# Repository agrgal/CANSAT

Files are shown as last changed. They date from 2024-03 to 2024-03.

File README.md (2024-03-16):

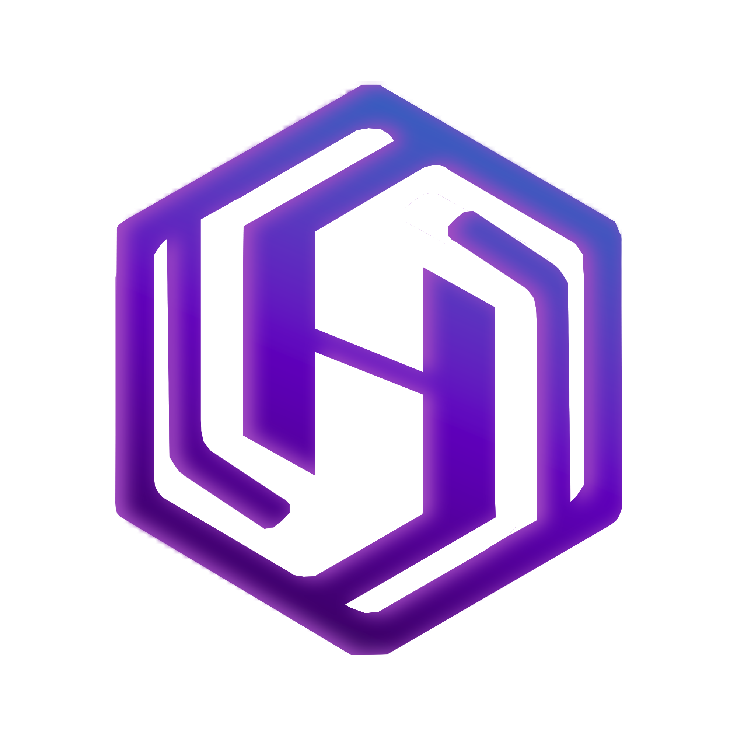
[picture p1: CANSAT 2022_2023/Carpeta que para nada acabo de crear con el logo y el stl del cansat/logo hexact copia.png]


# CANSAT - A4I y HEXACT
Proyectos CANSAT IES Seritium, año 2022 y 2023, presentados a los lanzamientos en la comunidad autónoma de Andalucía en Coria del Río y Antequera. Copia pública

# Reconocimiento
[CANSAT IES Seritium](https://github.com/CANSAT) © 2023 by Alejandro Chacón, David González, Antonio Jesús Suarez, Adrián Durán, Miriam Ganaza, Iker Espinosa y Aurelio Gallardo is licensed under [CC BY-NC-SA 4.0 ](http://creativecommons.org/licenses/by-nc-sa/4.0/?ref=chooser-v1)

# ¿Qué es?
El proyecto CANSAT (HEXACT en 2023, A4I en 2022) llevado a cabo por los alumnos Alejandro Chacón, David González, Antonio Jesús Suarez, Adrián Durán, Miriam Ganaza e Iker Espinosa del IES Seritium. Como mentor, Aurelio Gallardo. 

# ¿Qué contiene este documento?
Informe crítico de diseño y todo aquel material elaborado para llevar a cabo el proyecto (diseño, pruebas, programación, informes, resultados) de nuestra participación en las pruebas andaluzas de los años 2022 y 2023

# Material gráfico
+ [Vídeo presentación del proyecto 2023](https://youtu.be/i_LCr1teCZs?si=MErtpM3VWjnIBio4)
+ [Lanzamiento Mayo 2023](https://www.youtube.com/watch?v=RIHoM7wkHl4)
+ [Noticia diario de Jerez](https://www.diariodejerez.es/jerez/IES-Seritium-Agencia-Espacial-Europea-cansat_0_1791421220.html)
+ [CANSAT 2022](https://www.seritium.es/wordpress/index.php/2022/03/24/proyecto-cansat-2022/)

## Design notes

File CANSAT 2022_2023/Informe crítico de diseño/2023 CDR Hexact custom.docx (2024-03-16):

# HEXACT -CDR

(Critical Design Review)

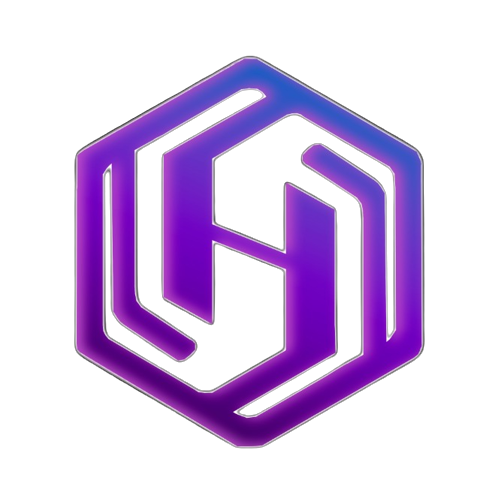
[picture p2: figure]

# Índice:

Índice: 1

Introducción: 2

El equipo: 2

Objetivos de la misión. 2

Vídeo presentación. 2

Misión primaria y secundaria. 3

Misión primaria. 3

Medida de presión y temperatura. 3

Diseño del paracaídas. 4

Análisis de datos 5

Diseño del CanSat 5

Misión secundaria 7

Dispersor de semillas. 7

Localización del dispositivo. 7

Planificación 8

Presupuesto 8

Plan de difusión y patrocinio 10

Notas 10

# Introducción:

## El equipo:

- Alejandro Chacón Pérez → Códigos del satélite y las estaciones tierra, diseño de la electrónica.
- David González Diosdado → Código processing, análisis de datos y ayuda en diseño en 3D.
- Antonio Jesús Suarez Gómez→ Diseño en 3D, soldadura y montaje de las antenas.
- Adrián Durán Perdigones→ Edición de los videos introductorios y diseño del logo.
- Miriam Ganaza Gómez→ Diseño y fabricación del paracaídas.
- Iker Espinosa Algeciras → Ayuda con las redes sociales.

Profesor responsable: Aurelio Gallardo (aurelio@seritium.es).

Instituto IES Seritium (11700767) - Jerez de la Frontera

## Objetivos de la misión.

Nuestros objetivos son:

1. Análisis con precisión de las condiciones medioambientales (Presión y temperatura) de la zona de lanzamiento.
2. Dispersión de semillas controlada durante el vuelo.
3. Análisis del estado del satélite durante el vuelo y recuperación para su reutilización una vez finalizada la misión.
4. Crear una base de datos didáctica para ayudar e incentivar a futuras generaciones de estudiantes que decidan participar en el proyecto CanSat.
5. Divertirnos y aprender.

## Vídeo presentación.

Vídeo presentación de nuestro proyecto CanSat. (https://youtu.be/FIYeHxksmDY)

# Misión primaria y secundaria.

El esquema de vuelo del proyecto se divide en 2 partes:

1. Recogida y procesamiento de datos, así como expulsión periódica de semillas, que toma lugar en el CanSat
2. Recibo y procesamiento de dichos datos, que incluye: Desencriptado, almacenamiento en la tarjeta SD, mostrado por pantalla y post-procesamiento en Processing para obtener la posición y tablas de los datos.

Los datos que recogeremos serán almacenados en la tarjeta SD, e incluyen: Temperatura, presión (y derivada, la altura), aceleración, ángulo de inclinación y distancia satélite-base.

Utilizamos, como placa procesadora, una ESP32 v4, que nos da una gran capacidad de procesamiento y un alto número de pines útiles. Elaboramos, asimismo, una PCB personalizada, que nos permite montar todos los sensores y componentes de manera segura y eficiente.

Para la estación de tierra, decidimos usar la placa de desarrollo LILYGO T-BEAM ESP32, que, además de proporcionarnos multitud de pines con los que trabajar, dispone, de manera integrada, de módulo de radio Lora y de chip GPS, muy útiles para el funcionamiento de muestras misiones primarias y secundarias.

Todo el proyecto, tanto el dispositivo CanSat como las estaciones de tierra, han sido programados en Arduino, usando la IDE 2.0.3 oficial.

## Misión primaria.

### Medida de presión y temperatura.

Como misión primaria, encontramos la medida de presión y temperatura. Conseguiremos estos datos con el sensor GY-87, ubicado en el interior de la carcasa del CanSat. A través del módulo LoRa de telecomunicaciones, enviamos los datos a las estaciones de tierra en forma de un sólo paquete con toda la información (Tanto de la misión primaria como secundaria) concatenada.

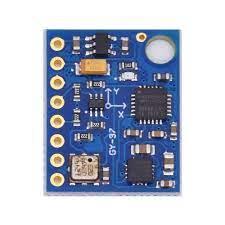
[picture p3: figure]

Elegimos este sensor porque, aparte de las medidas de temperatura y presión, nos proporciona también datos de aceleración y giroscopio, muy útiles para conocer el estado del satélite en su descenso, todo condensado en un sólo sensor.

Los programas siguen los siguientes esquemas. Diferenciamos entre el programa del satélite y el programa de las estaciones de tierra.

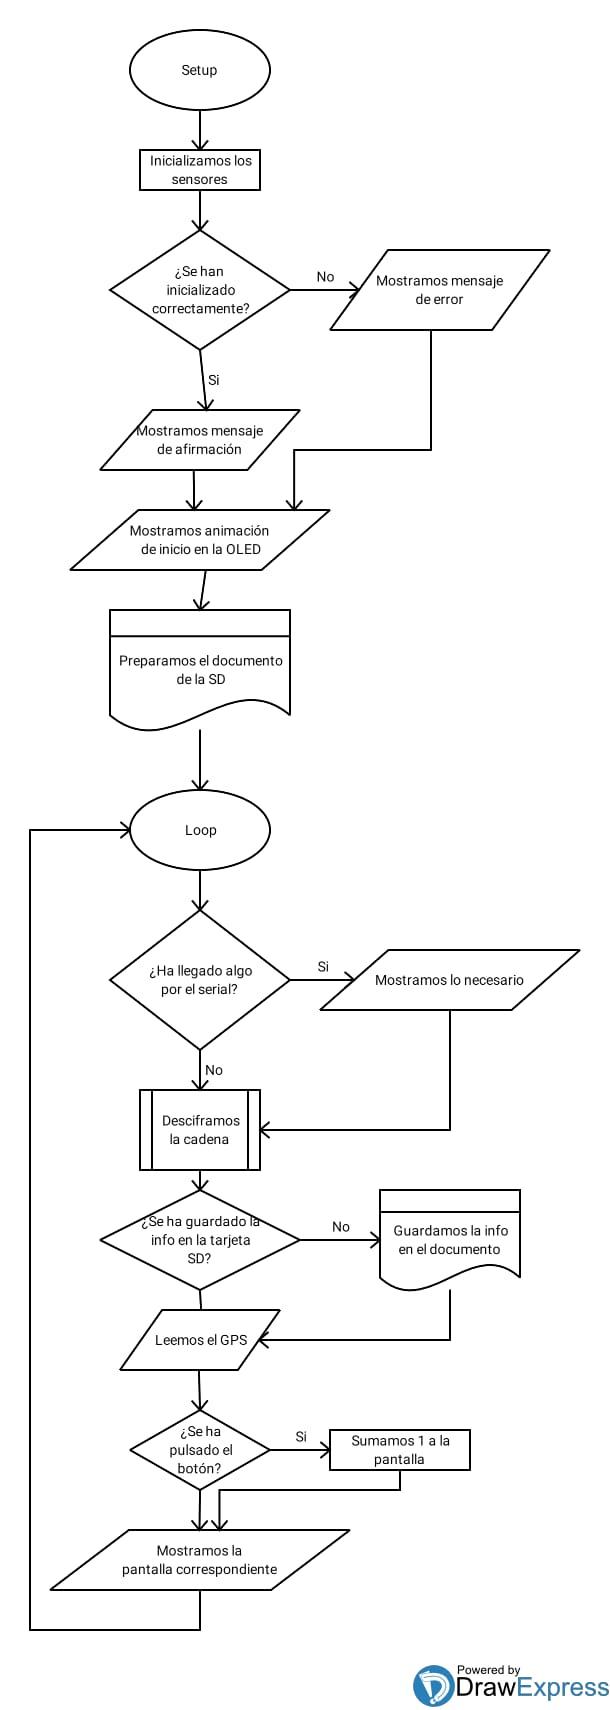
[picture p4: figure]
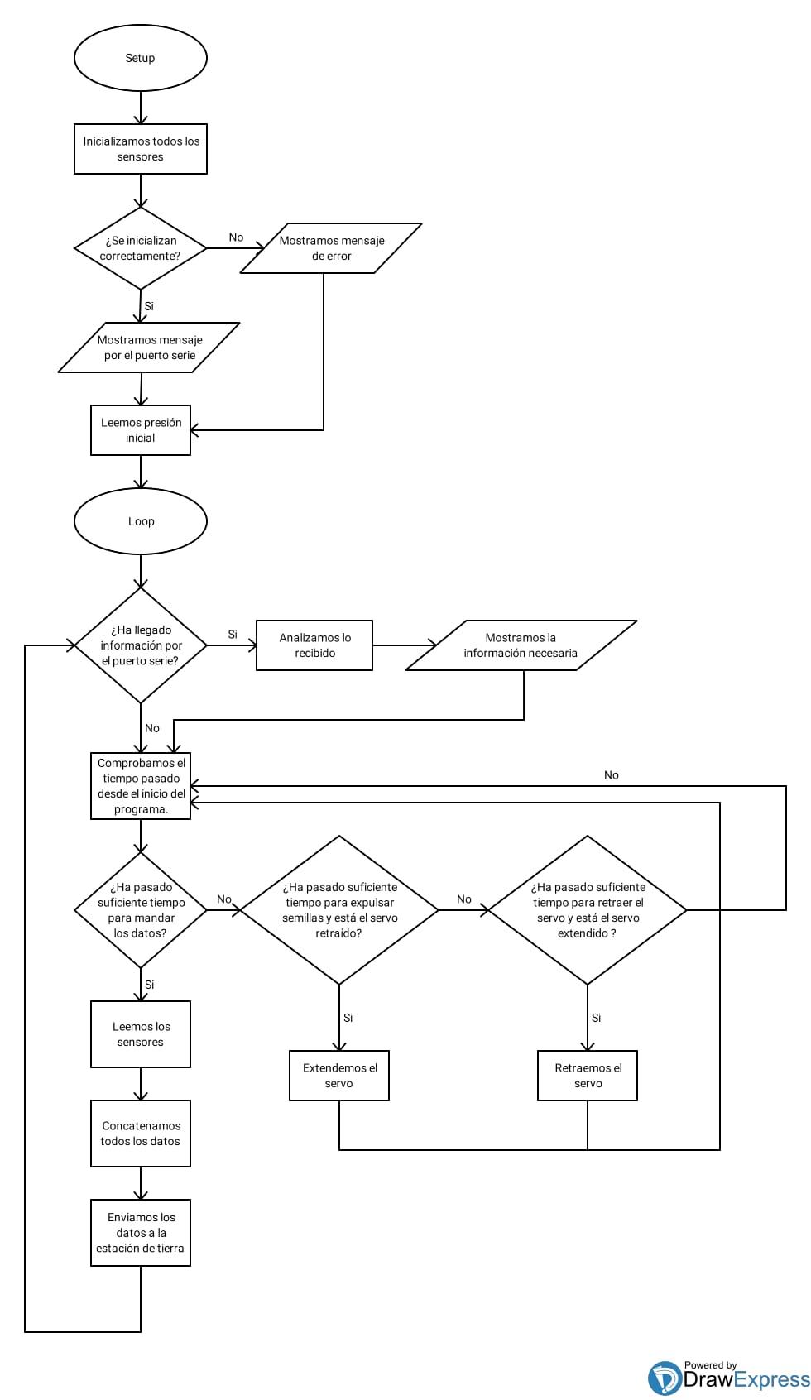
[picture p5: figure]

### Diseño del paracaídas.

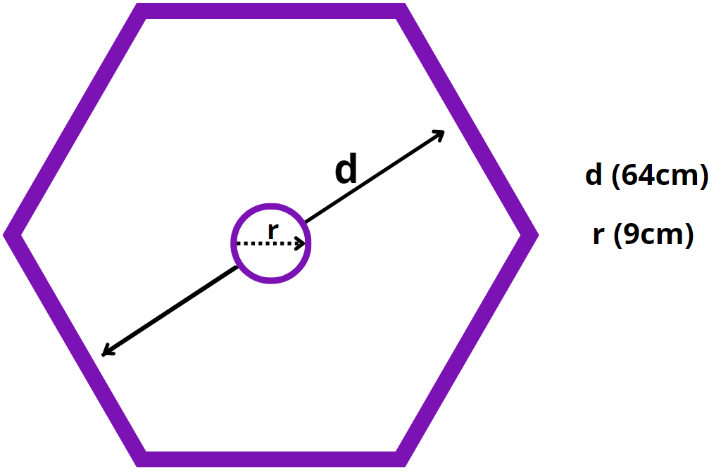
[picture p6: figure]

Teniendo como referencia nuestro proyecto CanSat de anteriores ediciones, decidimos rediseñar nuestro prototipo de paracaídas para que cayera de forma más rápida y precisa, aun conservando una velocidad regulada para evitar un impacto fatal.

El paracaídas está fabricado con tela especializada de paracaídas, con cuerda de tanza reforzada para unirla al CanSat. Sacamos la superficie necesaria para nuestro paracaídas igualando la fuerza gravitatoria con la de arrastre, teniendo en cuenta el peso deseado y la velocidad a la que queríamos que descendiese, para que nuestro aterrizaje sea rápido pero eficaz. Además, decidimos cambiar la forma anterior del paracaídas y hacerlo un hexágono, ya que así conseguimos reducir el uso de materiales aun sujetando la misma cantidad de peso.

### Análisis de datos

Los datos recogidos, una vez desencriptados y almacenados en la tarjeta SD de cada base, serán exportados al programa de Processing, que se encargará de mostrar, en distintas tablas 2D y 3D, los distintos datos, la posición mediante coordenadas, la angulación con un modelo 3d que se gira dependiendo de los datos recibidos y la presión y temperatura en una gráfica separada. Asimismo, y usando la distancia a cada estación, calcularemos la posición relativa del dispositivo, que se mostrará con los otros datos y será usada para la rápida y eficiente recuperación del CanSat. Estas son dos ejemplos de gráficas hechas con Processing con algunos datos de prueba:

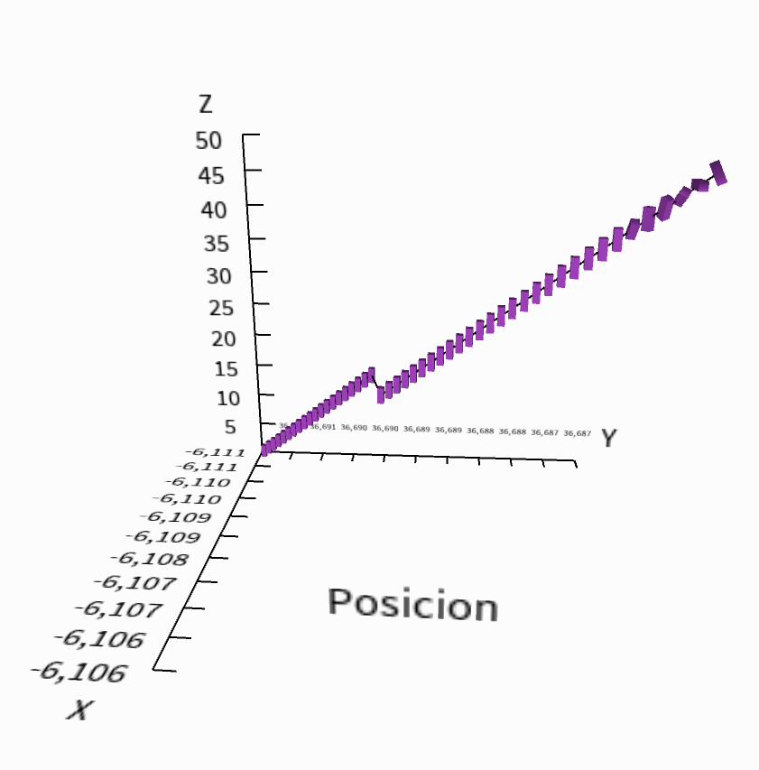
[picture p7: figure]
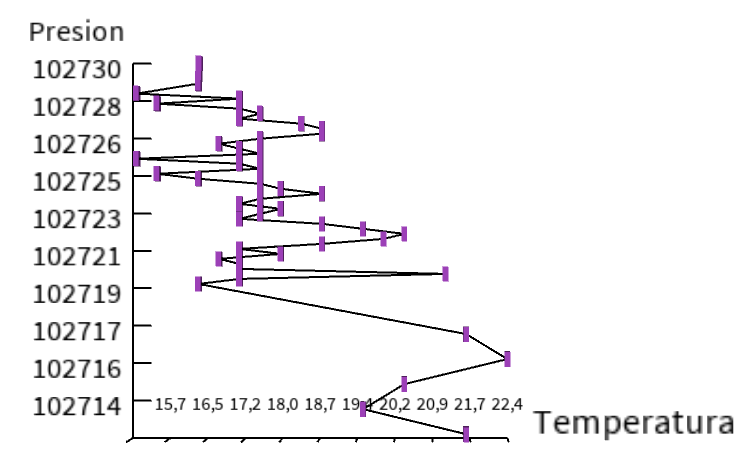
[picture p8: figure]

## Diseño del CanSat

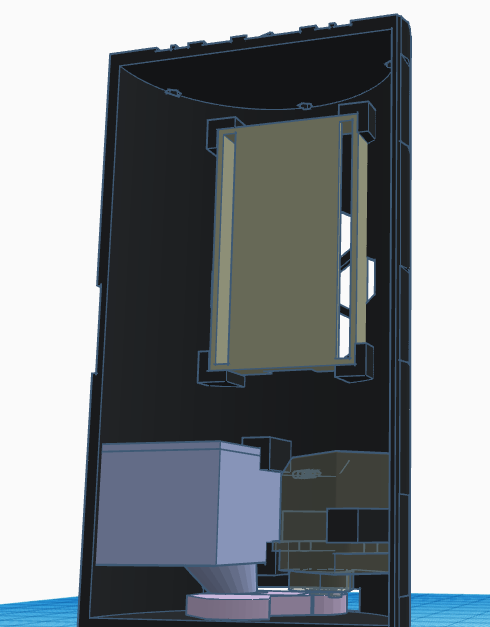
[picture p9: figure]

Peso aproximado: 312g , a falta de algunas modificaciones.

La carcasa de nuestro prototipo ha sido diseñada para dar cabida a los sensores, la placa ESP32, una batería 18650 y al mecanismo de eyección de semillas. La placa y los sensores están colocados en la parte superior, montados en la PCB personalizada en forma de “sandwich” (pieza colocada en el modelo color beige), para aprovechar al máximo el espacio útil. La PCB ha sido diseñada con esta configuración en mente, para posicionar los sensores y los pines de alimentación de la manera más eficiente posible.

En el centro de la PCB encontraremos el sistema de telecomunicaciones (Lora). En la parte inferior encontramos el servo (Transparente naranja), el cual mueve el brazo (rosa) que deja caer las semillas, depositadas desde el tanque (azul)

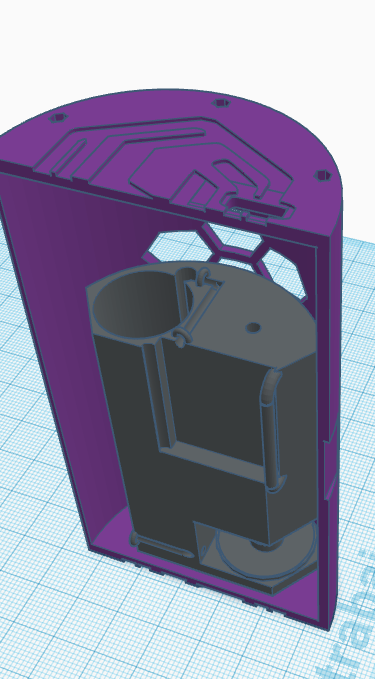
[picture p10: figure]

En la otra mitad encontraremos un modelo de donde va insertada la batería (18650), su respectivo módulo de carga ,y de forma perpendicular a la base, la antena que irá conectada al Lora. Estos componentes se encuentran en la mitad inferior para proporcionar más estabilidad durante el descenso, colocando la mayor cantidad de masa lo más bajo posible para alterar el centro de gravedad.

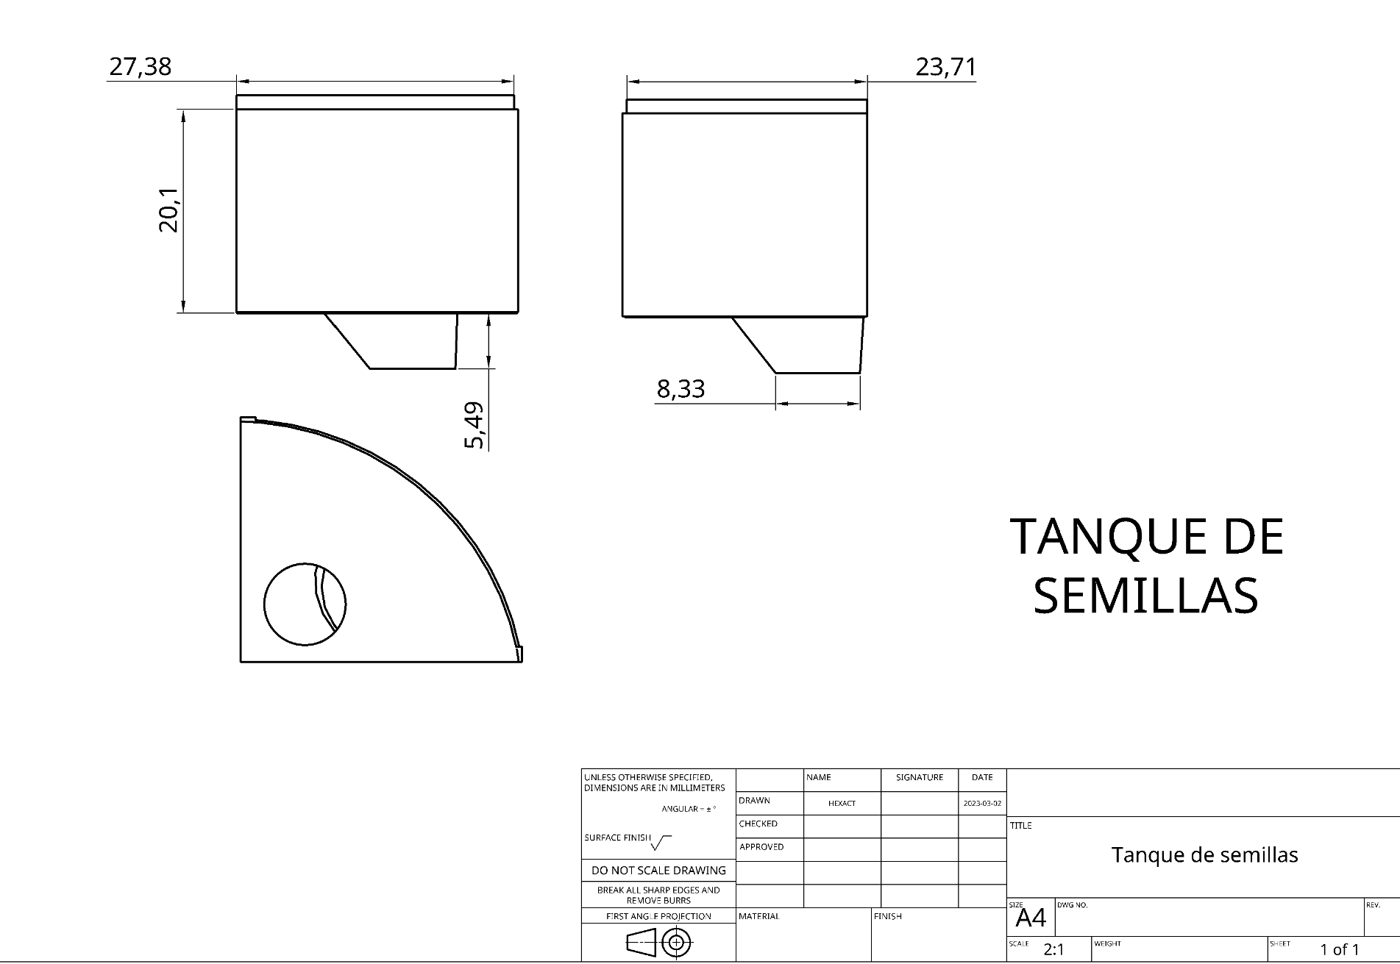
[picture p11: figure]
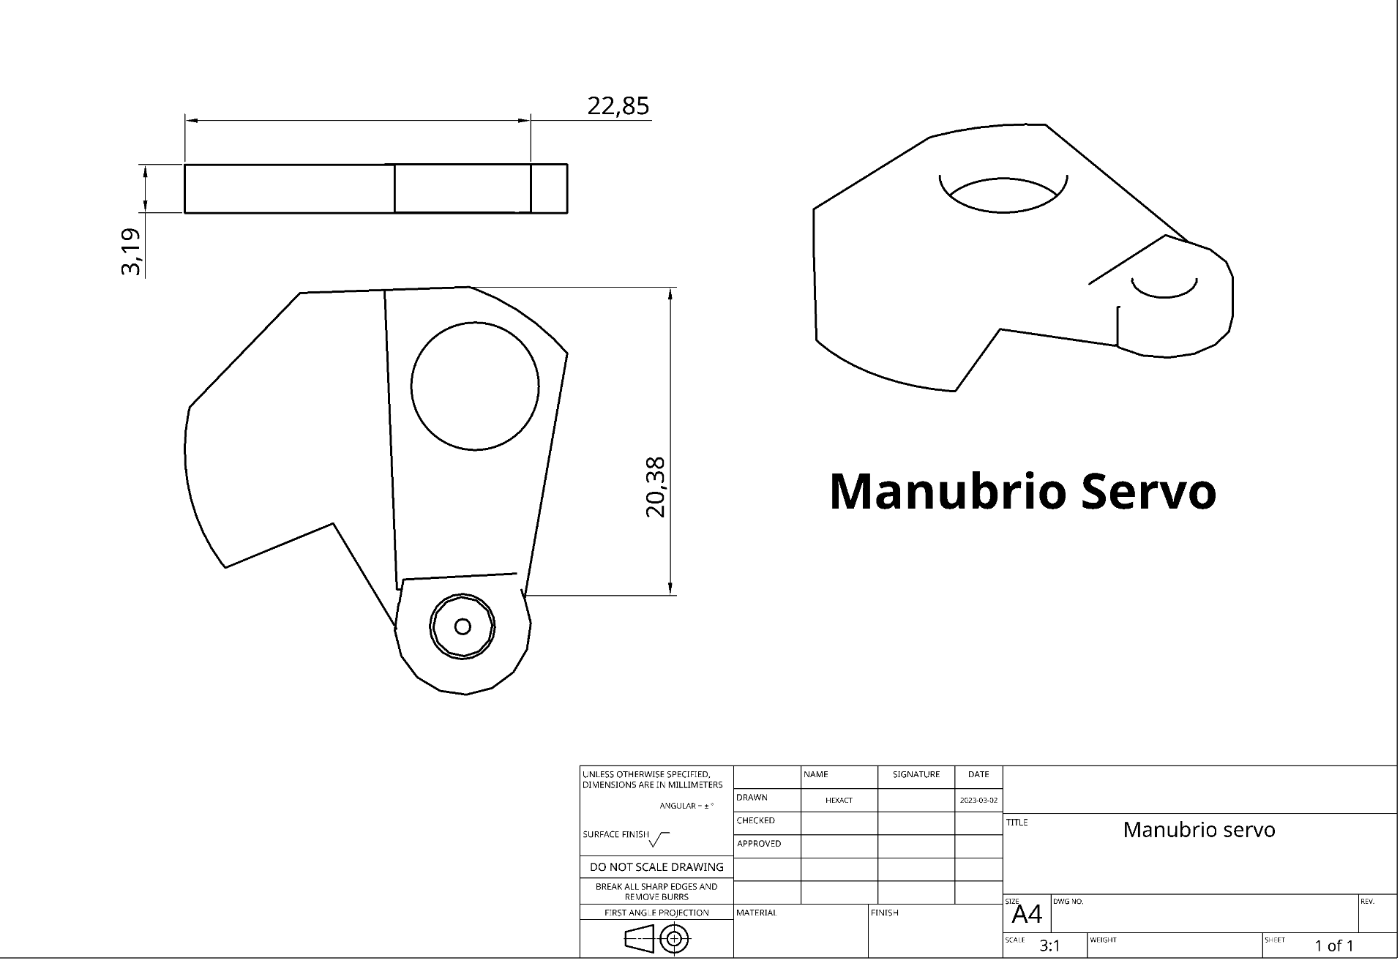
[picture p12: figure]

En los laterales exteriores, diseñamos unas hendiduras donde colocar bisagras metálicas, que proporcionan mayor resistencia al prototipo, aun manteniendo la funcionalidad de cofre.

El dispositivo está diseñado con facilidad de uso en mente: Dispondrá de salidas USB al exterior que permiten tanto recargar las baterías interiores como acceder a la placa directamente para su reprogramación o ajustes vía comunicación serie del propio programa. Lo ideamos todo para que pueda servir como base para futuras generaciones de participantes de CanSat y como elemento didáctico a la hora de enseñar programación, diseño y electrónica.

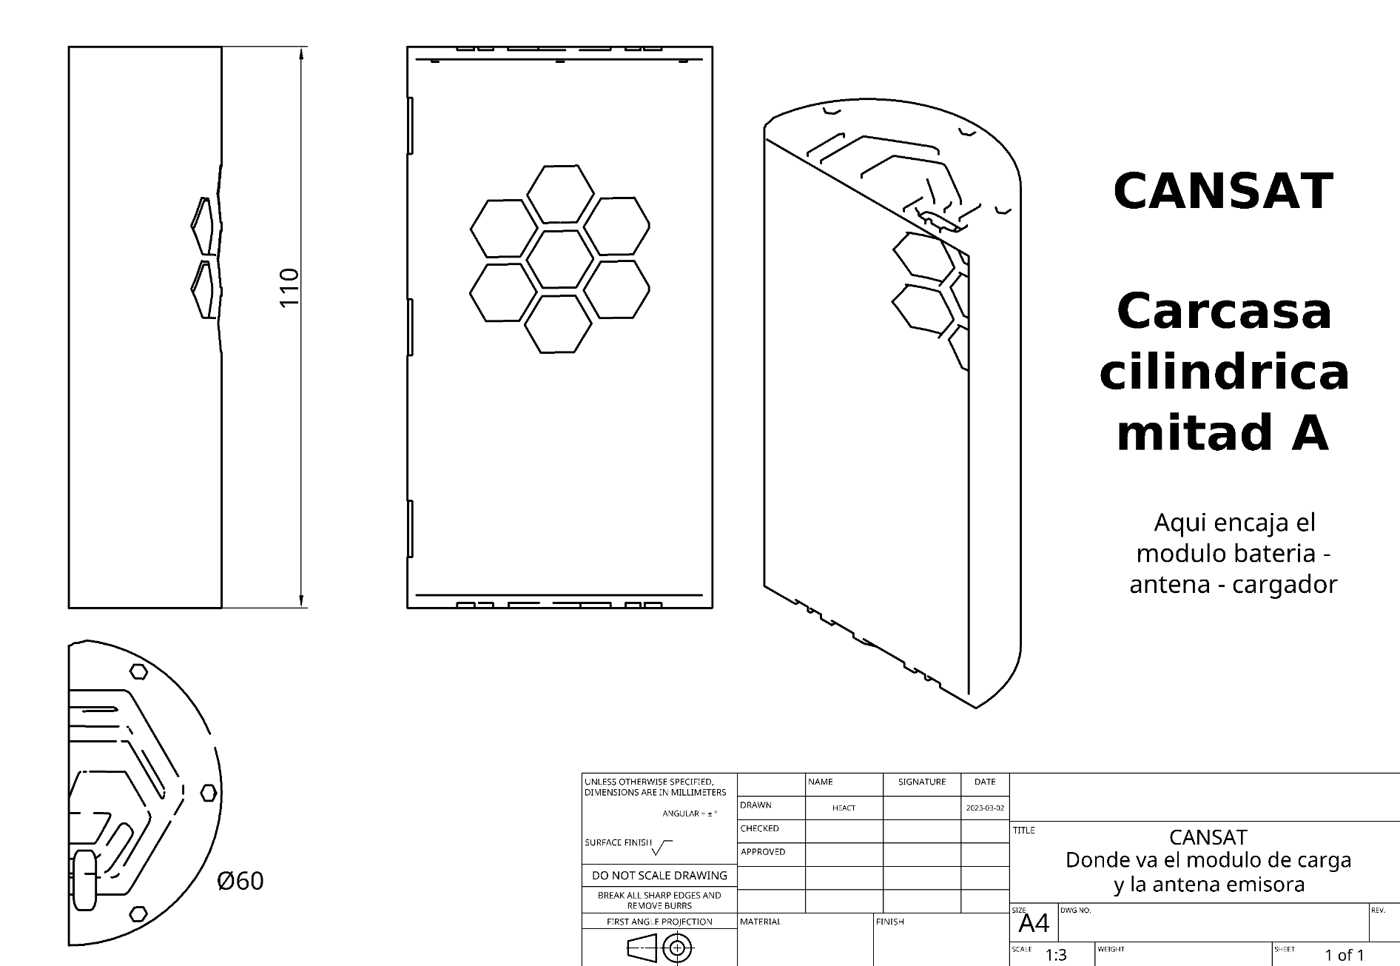
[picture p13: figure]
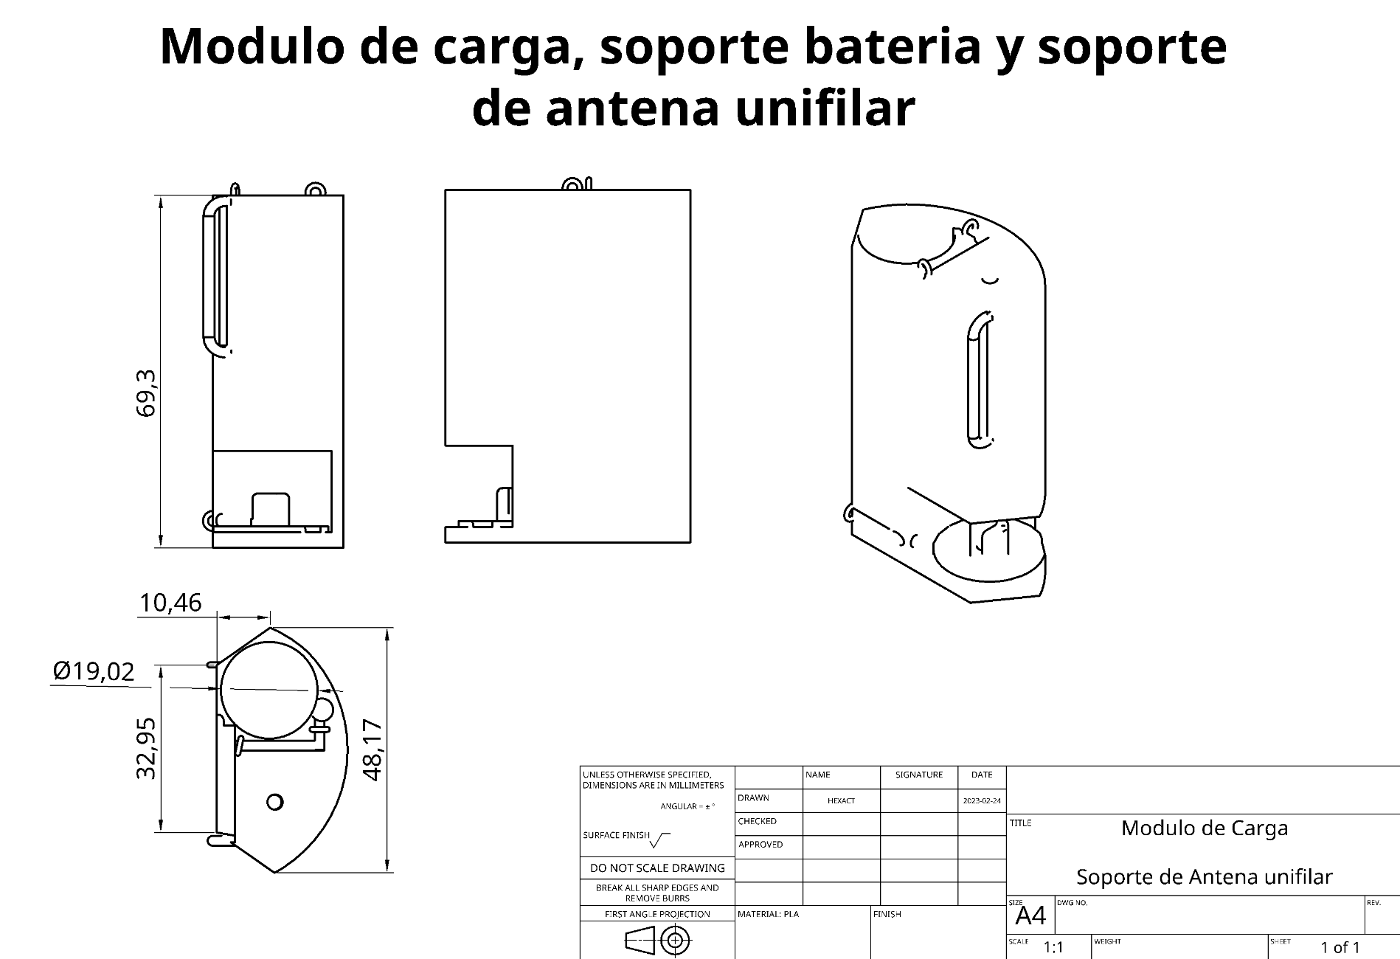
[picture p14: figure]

La antena también ha sido diseñada e impresa en 3D, con especial cuidado en mantener las medidas correctas para antenas Yagi pero con un diseño práctico: Está formada por partes desmontables para facilitar su almacenaje, y dispone de 2 mangos para poder sujetarla cómodamente .

## Misión secundaria

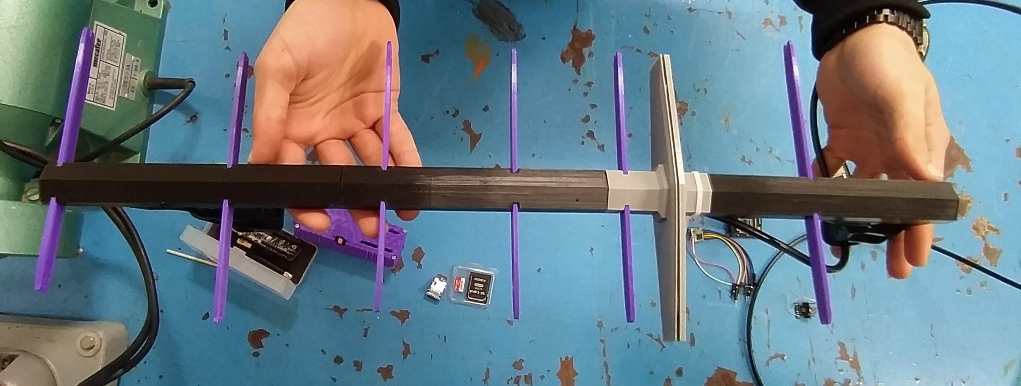
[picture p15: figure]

Nuestra misión secundaria se compone de 2 partes. La primera es un sistema de dispersión de semillas, que expulsa semillas periódicamente. Nuestro segundo proyecto científico es la localización del dispositivo sin uso de tecnologías GPS.

### Dispersor de semillas.

El sistema de dispersión de semillas consiste en un depósito con semillas, un brazo móvil y un servo que realiza el trabajo. Las semillas caen en el brazo por acción de la gravedad. El servo, periódicamente, se mueve, dejando caer las semillas al exterior.

### Localización del dispositivo.

Como segundo proyecto científico, hemos ideado un sistema de localización del dispositivo sin depender de sistemas GPS. Teniendo la experiencia de pasadas ediciones, y tras consultar expertos en el tema, aprendimos que, sometidos a altas aceleraciones, los chip GPS más extendidos en el mercado tienden a fallar. Por ello, y para facilitar la localización del prototipo, hemos optado por un sistema de trilateración basado en el RSSI (Received Signal Strength Indicator en inglés)

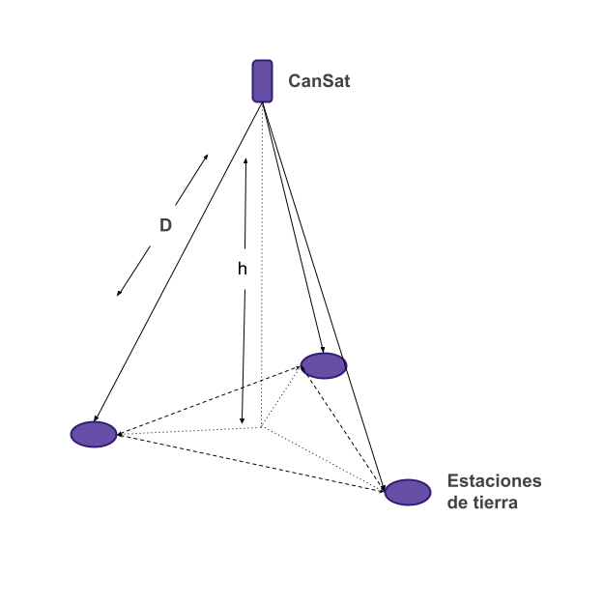
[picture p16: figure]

Una vez recibidas las cadenas por radiofrecuencia, tomamos la fuerza con la que llegan dichas señales (Fuerza que depende, entre otros factores, de la distancia entre el emisor y el receptor) y, usando una ecuación que obtuvimos de manera experimental (Anotando RSSIs y distancia emisor-receptor), obtenemos la distancia aproximada entre el dispositivo y nosotros.

Una vez tenemos esto, y teniendo 3 estaciones de tierra separadas, podemos triangular la posición del dispositivo. Tras hacer las operaciones, obtenemos la posición relativa, con la cual, apoyándonos con un GPS estable, podemos obtener la posición total o global del dispositivo con un margen de error pequeño.

# Planificación

Usamos unas 3 horas semanales en clase, más tiempo extra en casa, que varía dependiendo del trabajo de cada miembro del equipo, pero que rondan las 6-7 horas semanales.

- Finales de Octubre - Principios de Noviembre: Tormenta de ideas y comienzo del proyecto.
- Principios de Noviembre - Enero: Desarrollo de ambos programas, diseño en 3D de la antena y el CanSat, desarrollo del programa de análisis.
- Febrero: Desarrollo de las PCBs, primeras pruebas del paracaídas, antena y CanSat.
- Marzo en adelante: Perfeccionamiento del proyecto, pruebas finales y retoques extra

Debido a los estudios y a la inminente prueba de acceso a la universidad, intentamos realizar el trabajo lo antes posible, para dejar solo algunas pruebas para el final, por lo que el tiempo en casa ha ido disminuyendo a medida que el proyecto avanzaba. Sin embargo, esto último no ha hecho que descuidemos ningún aspecto del proyecto, manteniendo la calidad constante.

# Presupuesto

Muchos de los componentes electrónicos los tomamos del taller del centro, usando, para la carcasa y las antenas, las impresoras 3d, tanto las del centro como la personal de los alumnos. Muchas otras partes, como las baterías o el paracaídas, son recicladas de otros proyectos, lo cual ayuda a reducir tanto el presupuesto como el daño medioambiental.

Color verde: estaciones de tierra, Color azul: módulo CanSat, En blanco: material común y paracaídas. (*) Reusado del año pasado (**) Disponible en el taller (***) Reciclados de otros recursos.

Concepto | Valor / Observaciones | Cantidad | Precio (€)
TTGO T-Beam ESP32 WiFi GPS NEO-6M LoRa 868MHz | Estaciones Base: ESP32 y recepción de señales | 3 | 39,90 €
Módulo MicroSD Arduino | Grabar datos de las misiones primaria y secundaria | 3 | 1,5€
Tarjetas microSD | | 3 | 9€
Conector SMA | Construcción de antenas Yagi | 3 | 0,35€
Cable coaxial 50 Ohmios | | 3 | 3€
Alambre antenas (**) | | 3m | 1€
ESP32 | Módulo de Control | 1 | 4,29€
LORA 868MHz | SX1276 transmisión inalámbrica largo alcance | 1 | 12,57€
Placa PCB para el CANSAT | Placa para soldar | 1 | 15€
Módulo de carga y shields USB C | Conexiones | 1 | 2,5€
Mini Servo (**) | Misión secundaria | 1 | 2€
Batería Cansat 18650 LitoKala (*) | Fuente de energía | 1 | 5,4€
Baterias 18650 Samsung Para T-Beam(***) | Fuente de energía | 3 | 0€
Conmutador PCB (*) | Interruptor | 1 | 0,2€
Módulo Acelerómetro - Presión - Tª GY-87 (*) | Misión primaria y secundaria | 1 | 4,3€
Rollos PLA (**) | Color negro y morado 1Kg | 2 | 35.2€
Estaño, Tornillería, cables… | Valor aproximado | 1 | 1€
Bisagras | Estructura cierre | 4 | 0.01€
Tela paracaídas + tanza para los cordajes (*) | 1.5m2 + 1 rollo 20m | | 8.24€
COSTE TOTAL DEL PROYECTO EXCEPTUANDO ELEMENTOS REUSADOS O DE USO COMÚN EN EL TALLER: | | | 114.35€
COSTE TOTAL DEL PROYECTO: | | | 145.49€
ESTIMACIÓN TOTAL DEL PROYECTO + APROX. 15% GASTOS ENVÍO | | | 168.80€

# Plan de difusión y patrocinio

Como plan de difusión, hemos creado una cuenta de instagram (Hexact2023 ⬡ (https://www.instagram.com/hexact2023/)), en la que publicamos avances de nuestro proyecto.

Enlace al vídeo del proyecto publicado en YouTube: https://youtu.be/FIYeHxksmDY

Asimismo, pedimos patrocinio a diversas empresas, como Gnes, que nos apoyaron tanto económica como moralmente.

En estos tipos de proyectos es muy importante tener a empresas detrás nuestra que no solo aportan ayuda económica si no que también nos aportan su sabiduría, su apoyo y emplean toda su su confianza en un equipo.

Gnes es una empresa dedicada a la creación de células robóticas y cadena de montaje de mecanismos automovilísticos. Tras presentar el proyecto a trabajadores especializados en robótica, electrónica y software, se interesaron por el proyecto y nos dieron ciertos consejos referentes a diseño y funcionalidad, así como su enhorabuena.

Cada día buscamos más apoyo de más empresas, tiendas, centros, para tener ese respaldo económico y moral que se necesita en estos tipos de proyectos.

# Notas

Cabe destacar que, aún casi terminado, esta versión no es la versión definitiva. En las siguientes semanas, trabajaremos duro para seguir perfeccionando nuestro proyecto, y cabe la posibilidad de que añadamos más funciones simples o cambios en el diseño. Al fin y al cabo, pensamos que la clave de un proyecto como este reside en el perfeccionamiento e innovación constante, en búsqueda de nuevos retos con los que aprender y mejorar nuestro CanSat.

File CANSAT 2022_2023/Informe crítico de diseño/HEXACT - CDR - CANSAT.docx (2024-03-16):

HEXACT

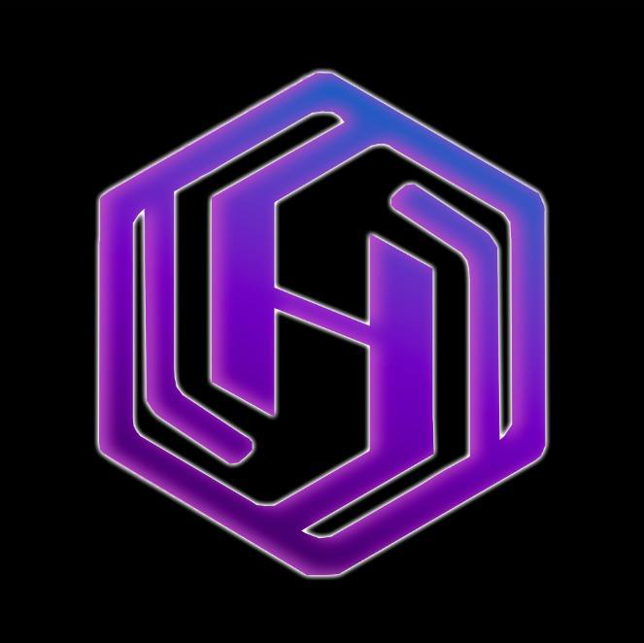
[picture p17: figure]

Critical DESIGN REVIEW

IES Seritium - HEXACT

Curso 2022-2023

Índice

Introducción 3

Organización y roles del equipo 3

Objetivos de la misión 3

Descripción del proyecto CANSAT 3

Esquema de la misión 3

Proyecto Científico 3

Diseño de la estructura 4

Paracaídas 4

Diseño eléctrico 5

Software 6

Sistema de recuperación 8

Estación de tierra 8

Planificación del proyecto CANSAT 8

Diagrama de GANTT (cronograma) 8

Presupuesto del CANSAT 9

Apoyo externo 10

Pruebas realizadas 10

Difusión del proyecto 10

Bibliografía / Referencias / Recursos 10

Anexos PROGRAMAS 11

= = = = = = = = = =

# Introducción

## Organización y roles del equipo

1. Adrián Durán Perdigones → Edición fotografía / vídeo. Grafismo.
2. Iker Espinosa Algeciras → Programación Processing y analista de datos. Responsable redes sociales y difusión.
3. Alejandro Chacón Pérez → Programación módulo CANSAT y estación tierra.
4. Antonio Jesús Suárez Gómez → Diseño 3D y construcción.
5. Miriam Ganaza Gómez → Programación Processing y analista de datos. Responsable paracaídas.
6. David González Diosdado → Programación Processing y analista de datos. Diseño 3D
7. Aurelio Gallardo Rodríguez → Profesores

Hemos dedicado 2h semanales, para no interrumpir nuestros estudios en la materia TIC. En clase dedicamos el tiempo en crear el programa de analítica en processing, creando el código de la placa, soldando cables, haciendo el paracaídas y realizando el guión y grabación de vídeos.

## Objetivos de la misión

1. Analizar con precisión el clima y terreno, mandar la información a la estación de tierra y analizarlo.
2. Aprender de telemetría, código, análisis, soldadura, ...
3. Pasarlo bien.

# Descripción del proyecto CANSAT

## Esquema de la misión

Los datos serán recogidos durante el lanzamiento y vuelo gracias a la telemetría por radio. Esperamos que todos los datos nos lo ofrezcan con la mayor exactitud y al momento; sabiendo a cuánta distancia está gracias a la intensidad de señal y llegando a una altura calculada suelte cada cierto tiempo semillas.

1. Misión primaria: Presión, temperatura, altura y telemetría.
2. Misión secundaria: Aceleración, giroscopio, posición según la intensidad de la señal y dispensador de semillas.

## Proyecto Científico

El dispensador de semillas tiene la función de plantar dónde y cuando nosotros queramos semillas en un campo o cultivo para hacerlo de forma automática y rápida.

Usamos la señal de telemetría para saber dónde está el Cansat al caer, el dispensador de semillas para cultivar árboles o plantas; presión, temperatura y altura para analizar el clima y realice una función de satélite; el acelerómetro para calcular la velocidad a la que se encuentra el Cansat y su posible orientación, y la telemetría para que nos llegue los datos en vivo.

## Diseño de la estructura (Antonio)

Planos de la estructura.

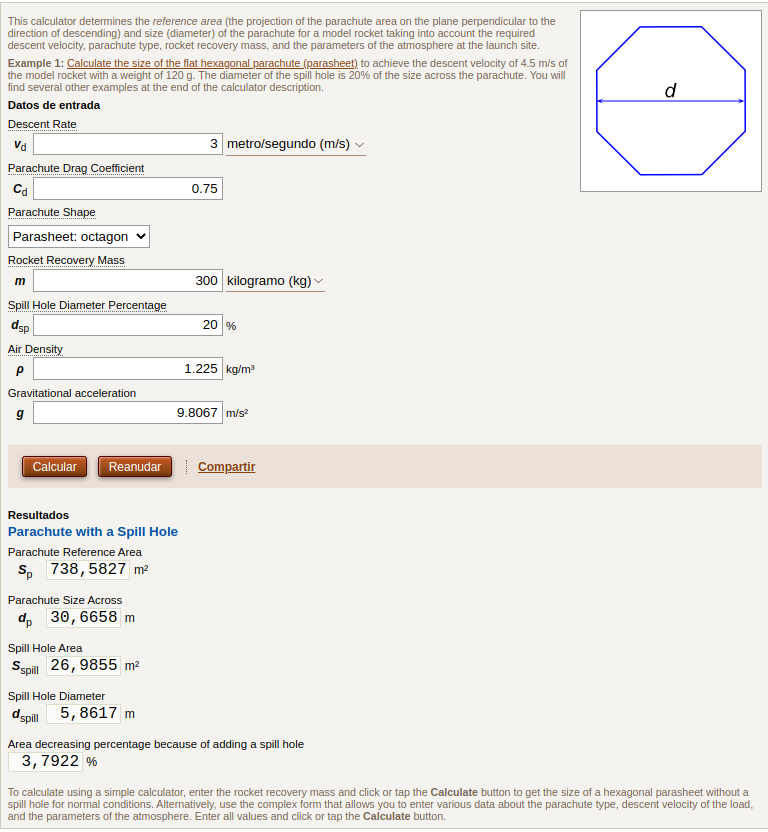
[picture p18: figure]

### Paracaídas (Miriam)

~~Cordaje: tanza 80LB (36.3Kgf). Tensión máxima que soporta.~~

~~Tela paracaídas: taffta nylon. 70D (unidades deniers) y entre 190/210T (trenzado de líneas horizontales/verticales). Tela especial para paracaídas y tiendas de campaña: ver bibliografía.~~

## Diseño eléctrico (Alejandro)

~~Más cosas que decir:~~

~~-Baterías.~~

~~-Módulo de carga.~~

~~-Placa hecha artesanal~~

~~-Componentes usados normalmente encontrados y no comprados.~~

~~Consumo teórico de componentes importantes:~~

- ~~Arduino Pro Mini: 200mA máximo en el chip~~
- ~~ESP32 CAM: 180mA sin flash~~
- ~~GY-87 (Acelerómetro): MPU6050 → 10 mA máximo. BMP180 → 1mA pico~~
- ~~LORA 868MHz: 130mA máximo transmitiendo~~
- ~~NEO6 GPS: 45mA~~
- ~~LED: menos de 70mA~~

~~I~~~~T~~ ~~teórico < 636mA~~

~~Consumo total de la placa en funcionamiento: I~~~~T~~ ~~= 220 mA max, medido con amperímetro, con LED encendido.~~

~~Carga de las pilas (tantalato litio):~~ Q = I⋅t = 3000mAh ⋅2= 6000 mAh ~~(). Con pilas estándar 18650,~~ Q = I⋅t = 2200mAh ⋅2= 4400 mAh

~~Tiempo de encendido teórico:~~ t > Q/I = 4400mAh/636mA = 6.9h ~~y~~ t > Q/I = 6000mAh/636mA = 9.4h ~~con pilas estándar y tantalato de litio, respectivamente.~~

~~Tiempo de encendido práctico:~~ t > Q/I = 4400mAh/ 200 mA = 22h y t > Q/I =6000mAh/ 200mA =60h

~~Enlaces a componentes; intensidades máximas teóricas:~~

~~-Arduino:~~ ~~https://components101.com/microcontrollers/arduino-pro-mini~~

~~-Módulo Lora:~~~~https://learn.sparkfun.com/tutorials/rfm69hcw-hookup-guide/all~~

~~-GY-87:~~ ~~MPU6050 → 10 mA máximo (~~~~https://www.elecrow.com/crowtail-mpu6050-accelerometer-gyro.html~~~~)~~

~~BMP180 → 1mA pico~~ ~~(~~~~https://components101.com/sensors/bmp180-atmospheric-pressure-sensor~~~~)~~

~~-ESP32 cam:~~~~https://loboris.eu/ESP32/ESP32-CAM%20Product%20Specification.pdf~~

~~-NEO6 GPS:~~~~https://lastminuteengineers.com/neo6m-gps-arduino-tutorial/~~

~~-Baterías:~~~~https://es.aliexpress.com/item/32835795441.html?gatewayAdapt=glo2esp&spm=a2g0o.order_list.0.0.21ef194dWV3ghg~~

Esquemático eléctrico / electrónico

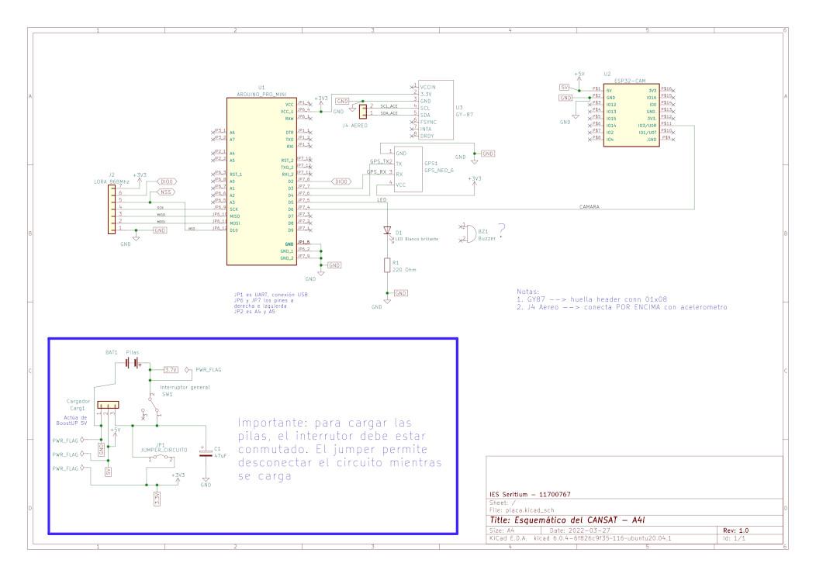
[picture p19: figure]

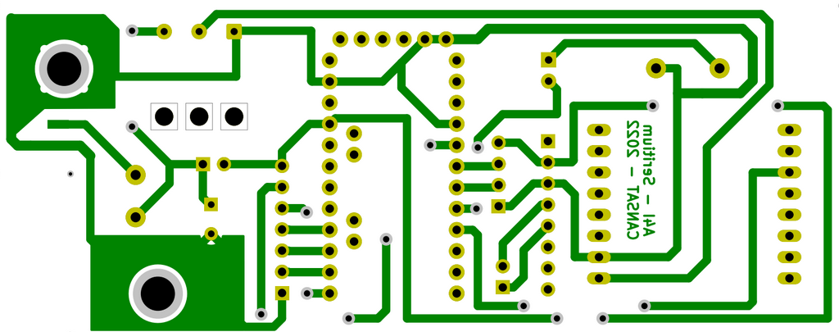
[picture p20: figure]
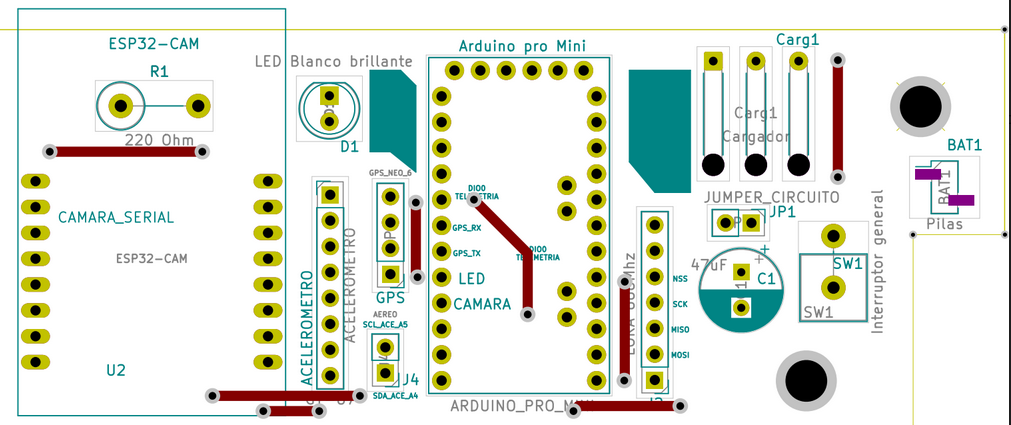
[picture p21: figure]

Pistas cobre | Serigrafía superior / puentes

## Sistema de recuperación

Para evitar cualquier daño en el gps o dificultad en el traspaso de datos hemos preferido usar la señal de telemetría para saber la distancia.

## Telemetría

El cansat tras recopilar los datos los envía al módulo lora el cual modula la señal a 868mHz y los envía por la antena.

## Estación de tierra

## Software

~~Hemos usado arduino como entorno de desarrollo, programando con su IDE oficial.~~

~~Para enviar a tierra los datos, los encriptamos y los enviamos mediante el módulo RFM69 a la estación de tierra. Los datos recopilados son divididos en 2 grupos,que se envían en dos cadenas distintas: La primera, con datos de aceleración y giros en los 3 ejes, presión (Y, derivada de esta, la altitud del CanSat), y temperatura; y la segunda, con datos de posicionamiento GPS y informe sobre si se ha tomado foto o no. ¿~~

Diagrama de flujo

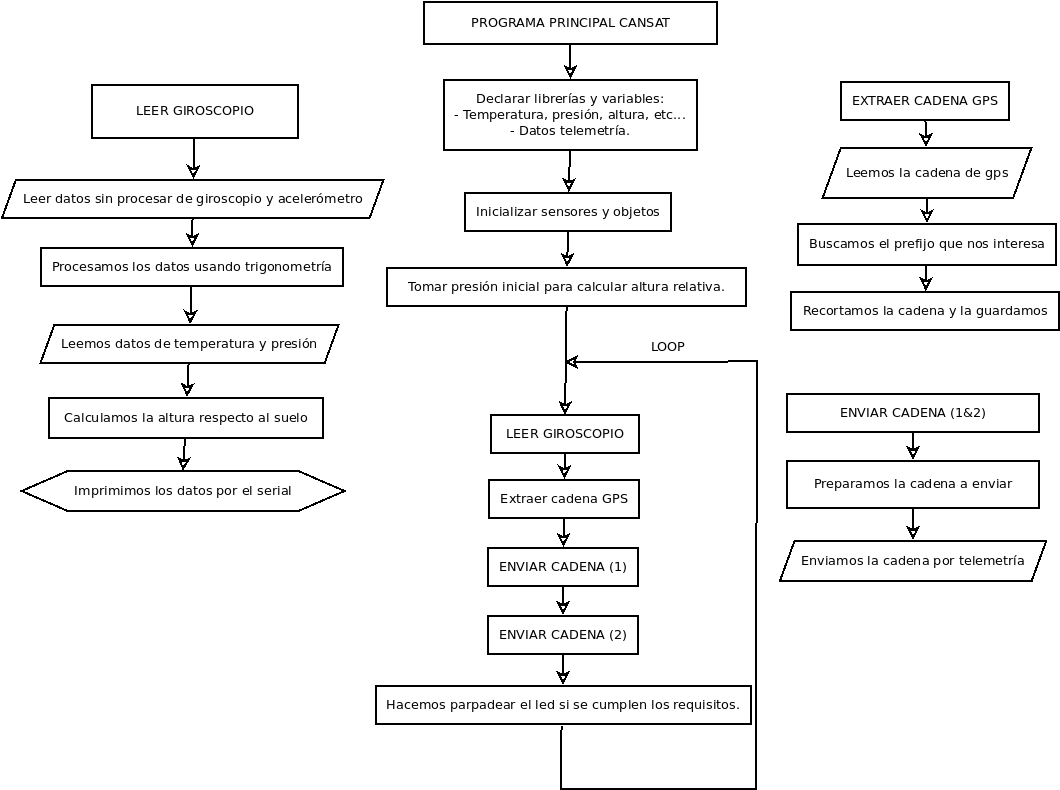
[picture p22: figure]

Estructura de datos

~~Seguir el enlace:~~ ~~https://docs.google.com/spreadsheets/d/1UBlOgZCoYUfe1Wo4PusJnSwNe_fxC9IOaQ9bJyCvJZQ/edit?usp=sharing~~

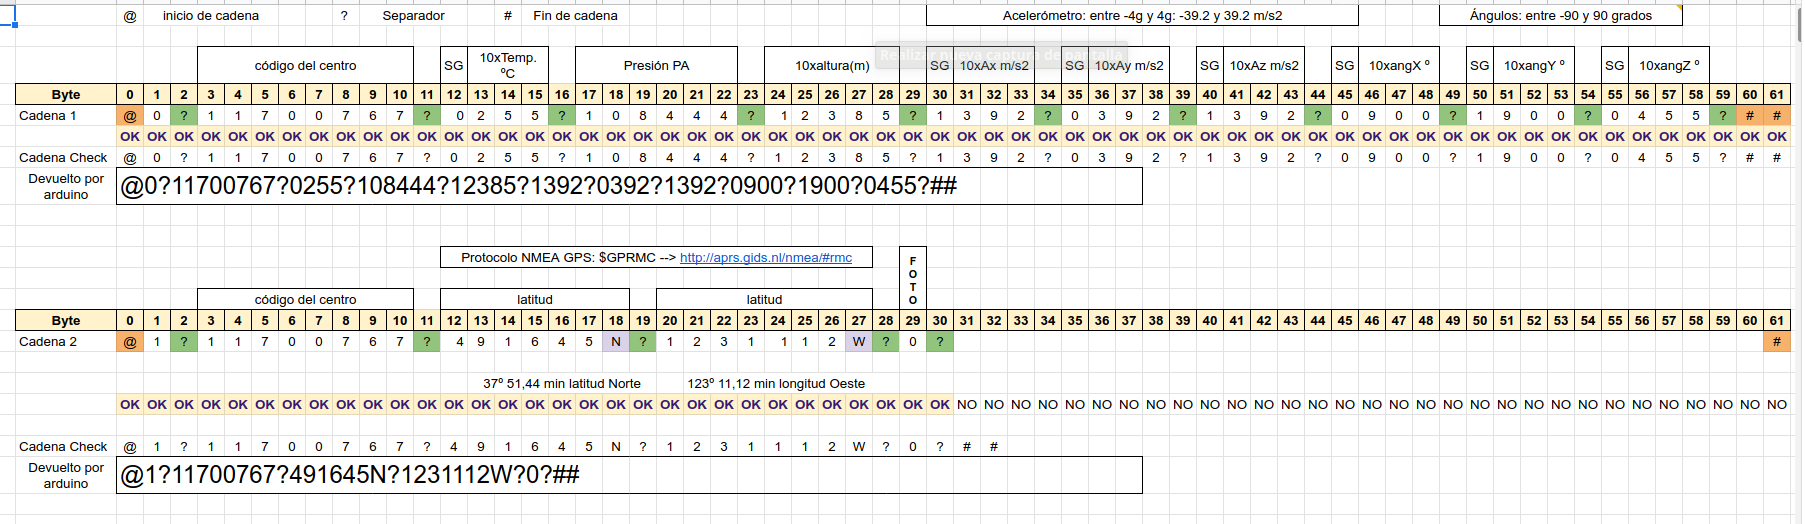
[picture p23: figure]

~~Se envían dos cadenas alternas. Descripción informaciones:~~

1. ~~Código de cadena, código del centro, temperatura ºC, presión PA, 10xaltura m, 10xAx, 10xAy, 10xAz (m/s2), 10xangX, 10xangY, 10xangZ (º)~~
2. ~~Código de cadena, código del centro,latitud, longitud, Si se ha tomado o no foto.~~

# Planificación del proyecto CANSAT

## Diagrama de GANTT (cronograma)

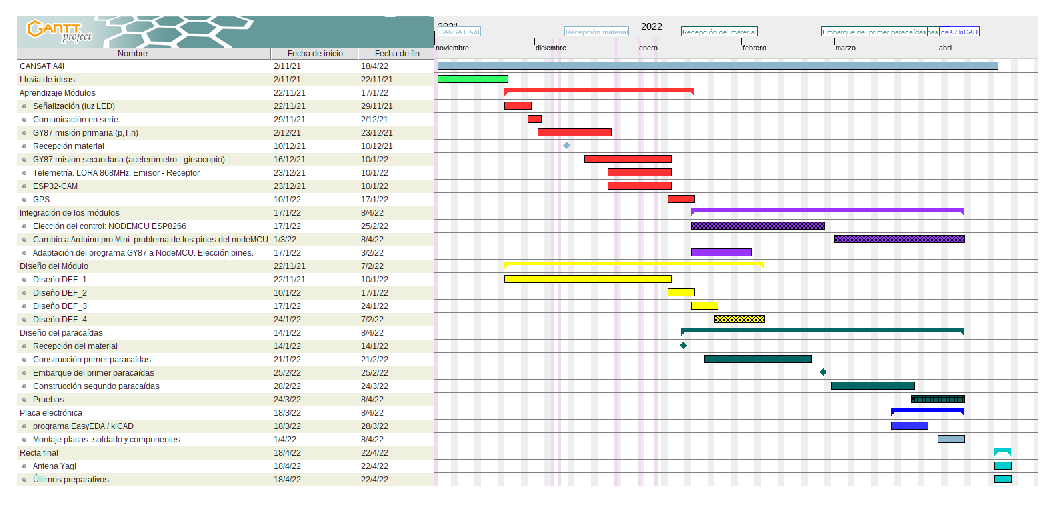
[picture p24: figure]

## Presupuesto del CANSAT

~~(*~~~~) Estación~~ ~~de tierra.~~

~~Concepto~~ | ~~Valor / Observaciones~~ | ~~Cantidad~~ | ~~Precio (€)~~
~~Led~~ | ~~Para señalización~~ | ~~1~~ | ~~0,01 €~~
~~Buzzer activo~~ | | ~~1~~ | ~~0,1 €~~
~~Interruptor~~ | ~~Mini para placa~~ | ~~1~~ | ~~0,01 €~~
~~Resistencia~~ | | ~~1~~ | ~~0,01 €~~
~~Cond. electrolítico~~ | ~~47uF~~ | ~~1+1(*)~~ | ~~0,02 €~~
~~NodeMCU V2~~ | ~~ESP8266~~ | ~~1 (*)~~ | ~~3 €~~
~~Arduino pro mini~~ | ~~Logic 3.3V~~ | ~~1~~ | ~~5 €~~
~~ESP32-CAM~~ | ~~Con cámara OV2640 75 mm 2MP~~ | ~~1~~ | ~~6€ + 3,5€ = 9,5€~~
~~LORA 868MHz~~ | | ~~1 + 1(*)~~ | ~~3€~~
~~GY-87~~ | ~~acelerómetro + giroscopio + presión + temperatura~~ | ~~1~~ | ~~5,5€~~
~~NEO6 GPS~~ | | ~~1~~ | ~~4€~~
~~Piezas 3D~~ ~~45g al 25% densidad + 56g al 50% = 101g~~ | ~~Habitáculo pilas (56g/50%)~~ | ~~1~~ | ~~PLA Amarillo 1 Kg a ~17€~~ ~~~1,7€~~
| ~~Separador~~ | ~~2~~
| ~~Tapa habitáculo pilas~~ | ~~1~~
| ~~Lateral A (Antena)~~ | ~~1~~
| ~~Lateral B~~ | ~~1~~
~~Tornillería, cableado, conectores. Estaño.~~ | ~~Disponibles en el taller~~ | ~~?~~ | ~~1€~~
~~Antena emisora y receptora, para CANSAT y estación tierra~~ | ~~Construidas con materiales del taller: arandelas y alma de cobre de cables de D1.5~~ | ~~2~~ | ~~2 x 0,5€ = 1 €~~
~~Placa electrónica~~ ~~41 x 104 mm~~ | ~~70 x 100 mm~~ | ~~1~~ | ~~1 €~~
~~Pilas 18650~~ | ~~Tantalato de litio~~ | ~~2~~ | ~~15,4€/ 2 = 7,7 €~~
Módulo de carga | Equivalente TP4056 | 1 | 0,5€
Tarjeta microSD | 32GB | 1 | 3€
Tela paracaídas | | 1 | 2,74 € x 1,5m2
Tanza pesca 4 hebras | | 1 | 5,5€
~~TOTAL:~~ | | | ~~55,29€~~

## Apoyo externo

~~En principio, hemos contado con recursos propios y material suministrado por los profesores.~~

## Pruebas realizadas

~~En el enlace:~~ ~~https://www.seritium.es/wordpress/index.php/2022/03/24/proyecto-cansat-2022/~~

# ~~Difusión del proyecto~~

1. ~~Página web:~~ ~~www.seritium.es~~
2. ~~Facebook:~~ ~~https://www.facebook.com/ies.seritium.jerez~~
3. ~~Twitter: @IesSeritium~~

# ~~Bibliografía / Referencias / Recursos~~

1. ~~Modelización del paracaídas:~~ ~~https://www.translatorscafe.com/unit-converter/es-ES/calculator/parachute-size/~~
2. ~~Cordaje paracaídas:~~ ~~https://es.aliexpress.com/item/1549494151.html?gatewayAdapt=glo2esp&spm=a2g0o.order_list.0.0.21ef194dWV3ghg~~
3. ~~GY-87:~~ ~~https://www.luisllamas.es/arduino-orientacion-imu-mpu-6050/~~ ~~,~~ ~~https://electropeak.com/learn/interfacing-gy-87-10dof-imu-mpu6050-hmc5883l-bmp085-module-with-arduino/~~~~,~~ ~~https://naylampmechatronics.com/blog/45_tutorial-mpu6050-acelerometro-y-giroscopio.html~~
4. ~~ESP32-CAM:~~ ~~https://randomnerdtutorials.com/esp32-cam-video-streaming-face-recognition-arduino-ide/~~
5. ~~Telemetría:~~ ~~https://learn.sparkfun.com/tutorials/rfm69hcw-hookup-guide/all~~~~,~~ ~~https://iot.uy/conectar-la-radio-rfm69-hcw-al-esp8266/~~~~,~~ ~~https://www.openhardware.io/view/171/Connecting-the-Radio~~~~,~~ ~~https://learn.adafruit.com/adafruit-rfm69hcw-and-rfm96-rfm95-rfm98-lora-packet-padio-breakouts/overview~~~~,~~ ~~https://forum.arduino.cc/t/nodemcu-and-rfm69hw-s2/599219/16~~
6. ~~GPS~~~~:~~ ~~https://www.luisllamas.es/localizacion-gps-con-arduino-y-los-modulos-gps-neo-6/~~
7. ~~Antena Yagi:~~ ~~https://www.changpuak.ch/electronics/yagi_uda_antenna_DL6WU.php~~

# Anexos PROGRAMAS

Programas en el emisor (satélite CANSAT)

/*** CanSat Unificado ***/

/* Programa unificado para el proyecto CanSat 2021/2022

* Dispositivo: Arduino Pro Mini (3.3v)

* Fecha: 8/1/2022

*/

/* -=- Por hacer -=-

* - Cámara así? Más pruebas?

*/

/* -=- Changelog -=-

* - 31/03/2022: Añadida la lectura de giro en el eje z. Añadido el envío de altura para la cámara. Limpieza de código.

* - 11/04/2022: Eliminada la función de envio de datos a la cámara. Por ahora lo dejamos así.

*/

/* -=- PINOUT -=-

* RX -----------3

* TX -----------4

* SDA ----------A4

* SCL ----------A5

* MOSI----------11

* MISO ---------12

* SCK ----------13

* NSS ----------10

* DIO0----------2

* ESP32-CAM-----6

*/

#include <RFM69.h>

#include <SPI.h>

#include <Adafruit_BMP085.h>

#include "I2Cdev.h"

#include "MPU6050.h"

#include "Wire.h"

#include <SoftwareSerial.h>

// Addresses for this node. CHANGE THESE FOR EACH NODE!

#define NETWORKID 100 // Must be the same for all nodes --> esta es la red.

#define MYNODEID 10 // My node ID --> este es el nodo de mi dispositivo

#define TONODEID 20 // Destination node ID --> este es el nodo del otro dispositivo

#define FREQUENCY RF69_868MHZ

#define FREQUENCY_E 868001000UL // frecuencia exacta

// AES encryption (or not):

#define ENCRYPT true // Set to "true" to use encryption

#define ENCRYPTKEY "123456789" // Use the same 16-byte key on all nodes --> clave secreta

// Use ACKnowledge when sending messages (or not):

#define USEACK false // Request ACKs or not

// Según la web https://iot.uy/conectar-la-radio-rfm69-hcw-al-esp8266/

#define SPI_CS 10 //NSS

#define IRQ_PIN 2 // DIO0

#define IRQ_NUM 2 //IRQ igual al pin

#define IS_RFM69HCW true // Si tu radio es RFM69HCW entonces va "true"

#define POWER_LEVEL 31 // Valor máximo de potencia

// -=- OBJETOS -=-

RFM69 radio = RFM69(SPI_CS, IRQ_PIN, IS_RFM69HCW, IRQ_NUM);

MPU6050 sensor; // Iniciamos sensor mpu6050

Adafruit_BMP085 bmp; // Iniciamos el BMP180

SoftwareSerial gps (3, 4); // Iniciamos el GPS (rxPIN, txPIN)

//SoftwareSerial cam(7, 6); // Iniciamos la comunicación con la cámara (Chequear pines)

const int led = 5;

// -=- DATOS A REGISTRAR -=-

// Cadena del GPS --> $GPRMC,225446,A,4916.45,N,12311.12,W,000.5,054.7,191194,020.3,E*68

String cadenaGPS = ""; // Cadena GPS

const unsigned int codigoSeritium = 11700767; // Código del centro

float temperatura = -99.9; // Ejemplo de temperatura con signo (2 dígitos + 1 decimal)

unsigned int presion = 999999; // Ejemplo de presión atmosférica. Entero positivo sin decimales.

float altura = 9999.9; // Ejemplo de altura. Positivo sin signo (4 dígitos + 1 decimal)

float alturaPrev = 9999.9;

float ace[3] = {+39.2,-39.2,+39.2}; // valores entre -4g y 4g, en m/s2. Con signo (2 dígitos + 1 decimal)

float ang[3] = {-90.0,+90.0,-45.5}; // valores entre -90 y 90, en grados. Con signo (2 dígitos + 1 decimal)

bool foto = false; // Si el programa ha tomado o no fotografías.

// -=- DATOS DEL GIRSOCOPIO -=-

short int ax, ay, az;

short int gx, gy, gz; // Valores sin procesar del acelarómetro y giroscopio.

long p0; // Valor de la presión inicial.

long tiempo_prev;

float dt; // Variables que calculan el tiempo (Cálculos aceleromtro/giroscopio)

float ang_x, ang_y, ang_z;

float ang_x_prev, ang_y_prev, ang_z_prev; // Variables para calcular los ángulos relativos de rotación.

//-=- Variables para el LED

unsigned long t = 0;

// ======================

// SETUP

// ======================

void setup() {

delay(2000);

pinMode(led, OUTPUT);

Serial.begin(9600);

Serial.print("Node ");

Serial.print(MYNODEID,DEC);

Serial.println(" ready");

Wire.begin();

gps.begin(9600);

//cam.begin(115200);

sensor.initialize();

if(sensor.testConnection()){

Serial.println("Sensor MPU6050 iniciado correctamente");

}

else{

Serial.println("Error al iniciar el sensor MPU6050");

}

if(!bmp.begin()){

Serial.print("Error al iniciar el sensor BMP180");

}

else{

Serial.println("Sensor BMP180 iniciado correctamente");

} //Inicializamos comunicación Serial y ambos sensores.

p0 = bmp.readPressure();

Serial.print("Presión inicial = ");

Serial.println(p0);

Serial.println("------------------------------------------"); //Tomamos la presión inical, que usaremos para calcular la altura.

radio.initialize(FREQUENCY, MYNODEID, NETWORKID);

radio.setHighPower(); // Always use this for RFM69HCW

// afinar frecuencia

radio.setFrequency(FREQUENCY_E);

// Saber más en: https://www.aprendiendoarduino.com/tag/banda-ism/

// rango de 863 a 870 MHz

// Turn on encryption if desired:

if (ENCRYPT) {

radio.encrypt(ENCRYPTKEY); }

Serial.println("Terminado SETUP...");

}

// ======================

// LOOP

// ======================

void loop() {

leerGY87();

extraerCadenaGPS();

delay(800); // Cada 500 milisegundos

enviarDatos(cadenaParaEnviar(1)); // Primero llama a la funcion cadenaParaEnviar con valor 1,

// que formatea los datos de temperatura, presión, altura, aceleración, ángulos.

// Los concatena en una cadena que empieza por @ y termina por #. Tamaño máximo 61 caracteres.

// Al principio incluye un 0, primer dato, y separado por ? el código del centro IES Seritium,

// Posteriormente, separado por ?, el resto de los datos. Acaba con #

delay(800); // cada 500 milisegundos

enviarDatos(cadenaParaEnviar(2)); // Idem caso anterior pero con valor 2.

// envía la latitud, la longitud y si se ha sacado o no foto.

t = millis();

digitalWrite(led, ((t/2500)%2)*((t/200)%2)*(altura<= 100)); //Hace parpadear al LED 2 veces cada 10 segundos.

//if(((int(altura) /*% 10*/) == 0)/* and (altura =! alturaPrev) and (altura >30)*/){ //Envio de datos de altura a la cámara.

/*if((t % 20000) == 0){

cam.print(0);

cam.flush();

alturaPrev = altura;

}*/

digitalWrite(6, LOW);

}

// ======================

// Funciones

// ======================

// ********************************

// Enviando cadena

// ********************************

void enviarDatos(String datos) {

// Envío de datos

static char sendbuffer[62];

static int sendlength = 0;

sendlength = datos.length();

datos.toCharArray(sendbuffer,sendlength);

Serial.println(datos);

if (USEACK){

if (radio.sendWithRetry(TONODEID, sendbuffer, sendlength))

Serial.println("ACK received!");

else

Serial.println("no ACK received");

}

// If you don't need acknowledgements, just use send():

else // don't use ACK

{

radio.send(TONODEID, sendbuffer, sendlength);

Serial.println("Enviado...");

}

sendlength=0;

}

void leerGY87(){

sensor.getAcceleration(&ax, &ay, &az);

sensor.getRotation(&gx, &gy, &gz); //Obtenemos las lecturas de aceleración y girsocopio.

dt = (millis()-tiempo_prev)/1000.0;

tiempo_prev = millis(); //Calculamos el tiempo pasado entre cada medición.

float ang_x_accel = atan(ax/sqrt(pow(ay,2) + pow(az,2)))*(180.0/3.14);

float ang_y_accel = atan(ay/sqrt(pow(az,2) + pow(ax,2)))*(180.0/3.14);

float ang_z_accel = atan(az/sqrt(pow(ax,2) + pow(ay,2)))*(180.0/3.14); //Calculamos los angulos de inclinación en los ejes usando el acelerómetro.

ang_x = 0.98*(ang_x_prev+(gx/131)*dt) + 0.02*ang_x_accel;

ang_y = 0.98*(ang_y_prev+(gy/131)*dt) + 0.02*ang_y_accel;

ang_z = 0.98*(ang_z_prev+(gy/131)*dt) + 0.02*ang_z_accel; //Calculamos la rotación usando tanto el girsocopio como el acelerómetro para eliminar errores.

ang_x_prev = ang_x;

ang_y_prev = ang_y;

ang_z_prev = ang_z;

ace[2] = az * (9.81/16384.0);

ace[1] = ay * (9.81/16384.0);

ace[0] = ax * (9.81/16384.0); //Calculamos la aceleración en m/s2 en los tres ejes

ang[0] = ang_x_accel;

ang[1] = ang_y_accel;

ang[2] = ang_z_accel;

altura = bmp.readAltitude(p0);

presion = bmp.readPressure();

//float m_az_ax = sqrt(pow(sqrt((pow(ax_ms2, 2)) + (pow(az_ms2, 2))), 2) + (pow(ay_ms2, 2))); //Calculamos el módulo de los 3 vectores, para así obtener la aceleración que experimenta.--> NO SE USA POR AHORA.

Serial.print("Rotación en X: ");

Serial.print(ang[0]);

Serial.print("º\tRotación en Y: ");

Serial.print(ang[1]);

Serial.print("º \tAceleración de caída(m/s2): ");

Serial.print(ace[2]);

Serial.print("\tTemperatura = ");

temperatura = bmp.readTemperature();

Serial.print(temperatura);

Serial.print("ºC\tPresión = ");

Serial.print(presion);

Serial.print("\tAltitud respecto al suelo = ");

Serial.print(altura);

Serial.println("m"); //Mostramos por puerto serie los datos obtenidos.

}

void extraerCadenaGPS(){

if(gps.available()){

String cadenaFinal = gps.readStringUntil('\n'); //Leemos lo que nos ha llegado hasta el salto de línea.

if (cadenaFinal.startsWith("$GPRMC")) {

int pos = cadenaFinal.indexOf("$GPRMC"); //Si empieza por el código que queremos, pillamos la posición de inicio.

if (pos == 0) {

cadenaGPS = cadenaFinal;

Serial.println(cadenaFinal); //Si la posición es 1, significa que tenemos toda la cadena, así que la recortamos y la imprimimos.

}

}

}

}

// ********************************

// cadena ya formateada para enviar

// ********************************

String cadenaParaEnviar (int cual) {

char tmp[62]; // variable de 62 bytes, del 0 al 61

switch (cual) {

// en este caso formateo los datos de temperatura, presión, altura, aceleración, ángulos.

case 1:

sprintf(tmp,"@%1d?%8d?%1d%3d?%6d?%5d?%1d%3d?%1d%3d?%1d%3d?%1d%3d?%1d%3d?%1d%3d?#",cual,codigoSeritium

,(temperatura>=0),(int) (abs(temperatura*10))

,presion,(int) (altura*10)

,(ace[0]>=0), (int) abs(ace[0]*10),(ace[1]>=0), (int) abs(ace[1]*10),(ace[2]>=0), (int) abs(ace[2]*10)

,(ang[0]>=0), (int) abs(ang[0]*10),(ang[1]>=0), (int) abs(ang[1]*10),(ang[2]>=0), (int) abs(ang[2]*10) );

break;

// en este caso envío los datos de latitud, longitud y si se ha sacado una foto

case 2:

sprintf(tmp,"@%1d?%8d?%6d%1s?%7d%1s?%1d?#",cual,codigoSeritium

,(int) ( 100.0 * parte(cadenaGPS,',',3).toFloat() ), parte(cadenaGPS,',',4)

,(int) ( 100.0 * parte(cadenaGPS,',',5).toFloat() ), parte(cadenaGPS,',',6)

,(int) foto);

// Serial.println(parte(cadenaGPS,',',0)); // importante usar simple quotas ' ' ' '

break;

// por defecto

default:

break;

}

return tmp; // devuelve el conjunto de caracteres

}

// ********************************

// encuentra parte de una cadena

// ********************************

String parte(String data, char separator, int index)

{

int found = 0;

int strIndex[] = {0, -1};

int maxIndex = data.length()-1;

for(int i=0; i<=maxIndex && found<=index; i++){

if(data.charAt(i)==separator || i==maxIndex){

found++;

strIndex[0] = strIndex[1]+1;

strIndex[1] = (i == maxIndex) ? i+1 : i;

}

}

return found>index ? data.substring(strIndex[0], strIndex[1]) : "";

}

===============================================

Programa en el receptor (estación TIERRA)

/*

* Ejemplo de envío de datos por telemetría

* Dispositivo: NodeMCU con valores lógicos a 3.3V

* Fecha: 8/1/2022

*/

// Include the RFM69 and SPI libraries:

#include <RFM69.h>

#include <SPI.h>

// Addresses for this node. CHANGE THESE FOR EACH NODE!

#define NETWORKID 100 // Must be the same for all nodes --> esta es la red.

#define MYNODEID 20 // My node ID --> este es el nodo de mi dispositivo

#define TONODEID 10 // Destination node ID --> este es el nodo del otro dispositivo

// RFM69 frequency, uncomment the frequency of your module:

//#define FREQUENCY RF69_433MHZ

// #define FREQUENCY RF69_915MHZ

#define FREQUENCY RF69_868MHZ

#define FREQUENCY_E 868001000UL // frecuencia exacta

// AES encryption (or not):

#define ENCRYPT true // Set to "true" to use encryption

#define ENCRYPTKEY "123456789" // Use the same 16-byte key on all nodes --> clave secreta

// Use ACKnowledge when sending messages (or not):

#define USEACK false // Request ACKs or not

// Packet sent/received indicator LED (optional):

// #define LED 9 // LED positive pin

// #define GND 8 // LED ground pin

// Según la web https://iot.uy/conectar-la-radio-rfm69-hcw-al-esp8266/

#define SPI_CS D8 //NSS o Cable Select al GPIO15 o D8

#define IRQ_PIN D1 // DIO0 conectado a GPIO4

#define IRQ_NUM D1 //IRQ igual al pin

#define IS_RFM69HCW true // Si tu radio es RFM69HCW entonces va "true"

#define POWER_LEVEL 31 // Valor máximo de potencia

// Create a library object for our RFM69HCW module:

RFM69 radio = RFM69(SPI_CS, IRQ_PIN, IS_RFM69HCW, IRQ_NUM);

// Datos que deben ser registrados

// GPS -->

String latitud ="";

String longitud="";

// Valores

unsigned int codigoSeritium = 0; // Código del centro

float temperatura = 0.0; // Ejemplo de temperatura con signo (2 dígitos + 1 decimal)

unsigned int presion = 0; // Ejemplo de presión atmosférica. Entero positivo sin decimales.

float altura = 0.0; // Ejemplo de altura. Positivo sin signo (4 dígitos + 1 decimal)

float ace[3] = {0.0, 0.0, 0.0}; // valores entre -4g y 4g, en m/s2. Con signo (2 dígitos + 1 decimal)

float ang[3] = {0.0, 0.0, 0.0}; // valores entre -90 y 90, en grados. Con signo (2 dígitos + 1 decimal)

bool foto = false; // Si el programa ha tomado o no fotografías.

// potencia recibida

int potencia = 0;

// ======================

// SETUP

// ======================

void setup() {

delay(2000);

Serial.begin(9600);

Serial.print("Node ");

Serial.print(MYNODEID,DEC);

Serial.println(" ready");

// Initialize the RFM69HCW:

// radio.setCS(10); //uncomment this if using Pro Micro

radio.initialize(FREQUENCY, MYNODEID, NETWORKID);

radio.setHighPower(); // Always use this for RFM69HCW

// afinar frecuencia

radio.setFrequency(FREQUENCY_E);

// Saber más en: https://www.aprendiendoarduino.com/tag/banda-ism/

// rango de 863 a 870 MHz

// Turn on encryption if desired:

if (ENCRYPT) {

radio.encrypt(ENCRYPTKEY); }

Serial.println("Terminado SETUP...");

}

// ======================

// LOOP

// ======================

void loop() {

delay(100); // tiene que ser más rápido que el envío de datos... Si se envían cada 500 ms, por ejemplo,

// aquí ponemos la mitad o así...

String cadena = recibirDatos();

if (cadena.length()>2) {analizaCadena(cadena); } // lama a la función que empieza a leer los datos.

} // Fin del LOOP

// ======================

// Funciones

// ======================

// ********************************

// Recibiendo cadena

// ********************************

String recibirDatos() {

char temp[63]; // un byte más de lo necesario

// String tmp;

if (radio.receiveDone()) // Got one!

{

// Print out the information:

// Serial.println( (int) radio.DATALEN);

// Serial.println(radio.DATA);

// The actual message is contained in the DATA array,

// and is DATALEN bytes in size:

for (byte i = 0; i < radio.DATALEN; i++) {

char n = (char)radio.DATA[i];

if (n=='#') {

temp[i]=NULL ; break;

} else if (n=='@') {

temp[i]='?';

} else {

temp[i]= n;

}

// Serial.print((char)radio.DATA[i]);

// Serial.print(temp[i]);

// tmp.concat(temp[i]);

}

// int bufferLength = sizeof(temp);

// Serial.println("Tamaño del buffer: " + (String) bufferLength);

// Serial.print("received from node ");

// Serial.print(radio.SENDERID, DEC);

// Serial.print(", message [");

// for (int j=0; j<bufferLength; j++) {

// Serial.print(temp[j]);

// }

// RSSI is the "Receive Signal Strength Indicator",

// smaller numbers mean higher power.

// Serial.print("], RSSI ");

// Serial.println(radio.RSSI);

potencia = (int) radio.RSSI;

// Send an ACK if requested.

// (You don't need this code if you're not using ACKs.)

if (radio.ACKRequested())

{

radio.sendACK();

Serial.println("ACK sent");

}

}

return String(temp);

// return tmp;

}

// ********************************

// análisis de cadena

// ********************************

void analizaCadena (String trama) {

String d; // dato que recibe

String comodin; // cadena comodin

d = parte(trama,'?',1); // debe recibir o un 1 o un 2

codigoSeritium = parte(trama,'?',2).toInt();

switch (d.toInt()) {

// recibo la primera cadena

case 1:

Serial.println("Potencia: " + (String) potencia + " // Cadena 1 --> " + trama);

Serial.println("Recibido para el centro: "+ (String) codigoSeritium);

// Temperatura

temperatura = recValorFloat (parte(trama,'?',3), 10, true); // cadena a recuperar, divisor, si tiene signo

// Presión

comodin = parte(trama,'?',4);

presion = comodin.toInt();

// Altura

altura = recValorFloat (parte(trama,'?',5), 10, false);

// Aceleracion

comodin ="Aceleraciones: ";

for (int i=0;i<3;i++) {

ace[i]=recValorFloat (parte(trama,'?',i+6), 10, true); // valores 6, 7 y 8

comodin = comodin + "A"+char(120+i)+" = "+ace[i]+" m/s2 ~ ";

}

comodin = comodin.substring(0,comodin.length()-2);

// Ángulos

comodin = comodin + "\nÁngulos: ";

for (int i=0;i<3;i++) {

ang[i]=recValorFloat (parte(trama,'?',i+9), 10, true); // valores 9, 10 y 11

comodin = comodin + "ANG"+char(120+i)+" = "+ang[i]+" º ~ ";

}

comodin = comodin.substring(0,comodin.length()-2);

// Muestra los datos en el monitor serie

Serial.println("T = "+(String) temperatura +" º C // "+

"P = "+(String) presion +" Pa // "+

"h = "+(String) altura +" m // ");

Serial.println(comodin);

break;

// ************************************************

// recibo la segunda cadena

case 2:

Serial.println("Potencia: " + (String) potencia + " // Cadena 2 --> " + trama);

Serial.println("Recibido para el centro: "+ (String) codigoSeritium);

// latitud

comodin = parte(trama,'?',3);

latitud = comodin.substring(0,2)+"º "+(String) recValorFloat(comodin.substring(2,6), 100, false)

+"' "+ cambioLetra(comodin.substring(6,7));

// longitud

comodin = parte(trama,'?',4);

longitud = comodin.substring(0,3)+"º "+(String) recValorFloat(comodin.substring(3,7), 100, false)

+"' "+ cambioLetra(comodin.substring(7,8));

// Fotografía

comodin = parte(trama,'?',5);

foto = (comodin=="1");

comodin = (foto) ? "Sí" : "No";

Serial.println("LAT: "+latitud+ " // LON: "+longitud);

Serial.println("¿Se ha tomado una foto?: "+ comodin);

break;

// *******************************************

default:

// Serial.println("No he encontrado una cadena: " + trama);

return; // sale de la función

break;

}

// imprime línea de caracteres

int iguales = 91;

while (--iguales) { Serial.print("="); }

Serial.print("\n");

}

// ********************************

// Recupera valores float

// ********************************

float recValorFloat (String num, int divisor, bool signo) {

float valor = 0.0;

int longitud = num.length();

if (signo) {

valor = num.substring(1,longitud).toFloat()/divisor;

valor = (num.substring(0,1)=="0") ? valor = -1*valor : valor;

} else {

valor = num.toFloat()/divisor;

}

return valor;

}

// ********************************

// cambio letra en longitud

// ********************************

String cambioLetra (String letra) {

return (letra=="W") ? "Oeste" : (letra=="E") ? "Este" : (letra=="N") ? "Norte" : (letra=="S") ? "Sur" : "" ;

}

// ********************************

// encuentra parte de una cadena

// ********************************

String parte(String data, char separator, int index)

{

int found = 0;

int strIndex[] = {0, -1};

int maxIndex = data.length()-1;

for(int i=0; i<=maxIndex && found<=index; i++){

if(data.charAt(i)==separator || i==maxIndex){

found++;

strIndex[0] = strIndex[1]+1;

strIndex[1] = (i == maxIndex) ? i+1 : i;

}

}

return found>index ? data.substring(strIndex[0], strIndex[1]) : "";

}

===============================================

Programa en el ESP32-CAM

#include "esp_camera.h"

#include "Arduino.h"

#include "FS.h" // SD Card ESP32

#include "SD_MMC.h" // SD Card ESP32

#include "soc/soc.h" // Disable brownour problems

#include "soc/rtc_cntl_reg.h" // Disable brownour problems

#include "driver/rtc_io.h"

#include <EEPROM.h> // read and write from flash memory

// define the number of bytes you want to access

#define EEPROM_SIZE 1

// Pin definition for CAMERA_MODEL_AI_THINKER

#define PWDN_GPIO_NUM 32

#define RESET_GPIO_NUM -1

#define XCLK_GPIO_NUM 0

#define SIOD_GPIO_NUM 26

#define SIOC_GPIO_NUM 27

#define Y9_GPIO_NUM 35

#define Y8_GPIO_NUM 34

#define Y7_GPIO_NUM 39

#define Y6_GPIO_NUM 36

#define Y5_GPIO_NUM 21

#define Y4_GPIO_NUM 19

#define Y3_GPIO_NUM 18

#define Y2_GPIO_NUM 5

#define VSYNC_GPIO_NUM 25

#define HREF_GPIO_NUM 23

#define PCLK_GPIO_NUM 22

int pictureNumber = 0;

void setup() {

WRITE_PERI_REG(RTC_CNTL_BROWN_OUT_REG, 0); //disable brownout detector

Serial.begin(115200);

pinMode(4, OUTPUT);

//Serial.setDebugOutput(true);

//Serial.println();

camera_config_t config;

config.ledc_channel = LEDC_CHANNEL_0;

config.ledc_timer = LEDC_TIMER_0;

config.pin_d0 = Y2_GPIO_NUM;

config.pin_d1 = Y3_GPIO_NUM;

config.pin_d2 = Y4_GPIO_NUM;

config.pin_d3 = Y5_GPIO_NUM;

config.pin_d4 = Y6_GPIO_NUM;

config.pin_d5 = Y7_GPIO_NUM;

config.pin_d6 = Y8_GPIO_NUM;

config.pin_d7 = Y9_GPIO_NUM;

config.pin_xclk = XCLK_GPIO_NUM;

config.pin_pclk = PCLK_GPIO_NUM;

config.pin_vsync = VSYNC_GPIO_NUM;

config.pin_href = HREF_GPIO_NUM;

config.pin_sscb_sda = SIOD_GPIO_NUM;

config.pin_sscb_scl = SIOC_GPIO_NUM;

config.pin_pwdn = PWDN_GPIO_NUM;

config.pin_reset = RESET_GPIO_NUM;

config.xclk_freq_hz = 20000000;

config.pixel_format = PIXFORMAT_JPEG;

if(psramFound()){

config.frame_size = FRAMESIZE_UXGA; // FRAMESIZE_ + QVGA|CIF|VGA|SVGA|XGA|SXGA|UXGA

config.jpeg_quality = 10;

config.fb_count = 2;

} else {

config.frame_size = FRAMESIZE_SVGA;

config.jpeg_quality = 12;

config.fb_count = 1;

}

// Init Camera

esp_err_t err = esp_camera_init(&config);

if (err != ESP_OK) {

Serial.printf("Camera init failed with error 0x%x", err);

return;

}

//Serial.println("Starting SD Card");

if(!SD_MMC.begin()){

Serial.println("SD Card Mount Failed");

return;

}

uint8_t cardType = SD_MMC.cardType();

if(cardType == CARD_NONE){

Serial.println("No SD Card attached");

return;

}

}

void loop() {

int t = millis();

if((t%10000) == 0){

camera_fb_t * fb = NULL; // Take Picture with Camera

fb = esp_camera_fb_get();

if(!fb) {

Serial.println("Camera capture failed");

return;

}

// initialize EEPROM with predefined size

//EEPROM.begin(EEPROM_SIZE);

//pictureNumber = EEPROM.read(0) + 1;

pictureNumber = t/10000;

// Path where new picture will be saved in SD Card

String path = "/picture" + String(pictureNumber) +".jpg";

fs::FS &fs = SD_MMC;

Serial.printf("Picture file name: %s\n", path.c_str());

File file = fs.open(path.c_str(), FILE_WRITE);

if(!file){

Serial.println("Failed to open file in writing mode");

}

else {

file.write(fb->buf, fb->len); // payload (image), payload length

Serial.printf("Saved file to path: %s\n", path.c_str());

//EEPROM.write(0, pictureNumber);

//EEPROM.commit();

}

file.close();

esp_camera_fb_return(fb);

// Turns off the ESP32-CAM white on-board LED (flash) connected to GPIO 4

digitalWrite(4, LOW);

}

}

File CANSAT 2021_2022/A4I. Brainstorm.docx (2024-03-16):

# Participante: ___________________________________

# Brainstorming

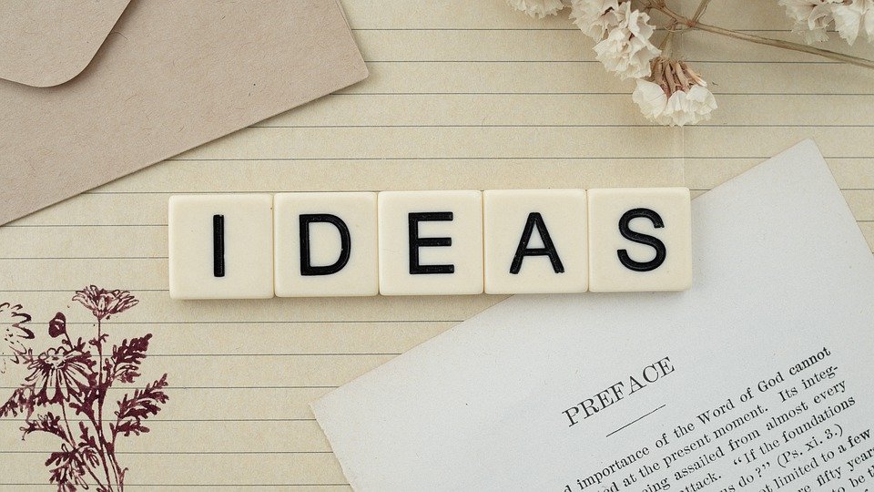
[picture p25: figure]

## 1.- Objetivos de este documento

A. Pensar, poner nuestras ideas en orden.
B. Contextualizar el proyecto A4I.¿Qué podemos hacer dentro de nuestras posibilidades? ¿Qué tenemos que tener en cuenta? ¿Qué elementos pueden ser más idóneos?

## 2.- Procedimiento

A. Cada miembro del equipo CANSAT tendrá que elaborar un boceto de sus ideas sobre el proyecto de forma individual. Conviene que no las consulte con ningún otro miembro del equipo (eso se hará en un paso posterior).
B. Importante: se deberá seguir el esquema de este documento. Deberá intentar cumplimentarlo en su totalidad y ser lo más detallado posible.
C. También pueden elaborar de forma voluntaria un boceto los padres/madres de los alumnos del proyecto y los profesores implicados en el mismo. Todas las ideas son bienvenidas.
D. Entrega: antes del 22-Noviembre-2021
E. Procedimiento de entrega: se entregará una copia de este documento en la carpeta siguiente. El participante deberá indicar su nombre en la portada. Importante: la entrega sólo será permitida si te has logueado con tu usuario del IES Seritium (los padres lo podrán hacer a través del correo de sus hijos).

CANSAT / lluvia de ideas / Entrega: https://drive.google.com/drive/folders/12hKpSoCbCRVf3Yd-O0-xGukdOw-d7Ar6?usp=sharing

## 3.- Subdivisión de la planificación

1. Funcionalidad
2. Boceto general del proyecto (dibujo). Materiales
3. Paracaídas.
4. Electrónica / electricidad.
  4.1. Unidad de control
  4.2. Alimentación
  4.3. Sensores u otros que capturen o manejen datos.
  4.4. Telemetría.
5. Programación.

# 1.- Funciones

Se trata de dar respuesta a la siguiente pregunta ¿Qué será capaz de hacer nuestro satélite?

Rellena la siguiente tabla con tus ideas en las filas en blanco (pongo ya las que son obligatorias).

N | Descripción | Magnitud relacionada (si existe) con la unidad de medición
1 | Medición de la temperatura del aire | T (º C)
2 | Medición de la presión atmosférica | p (¿atm?)
3 | Medición de la altura (¿directamente o calculada a través de la presión?) | h (m)
4 | Enviar datos de telemetría (antenas asociadas). Frecuencia por determinar, aunque probablemente 868MHz. Equipo de tierra que recoja los datos. | bitrate “bajo”
5 | Descender suavemente mediante paracaídas.
6 | Con algún sistema, debe indicar dónde está cuando aterrice (sonido, luz, GPS)
7 | Batería accesible con interruptor general.

# 2.- Boceto general.

Dibuja aquí tu idea general. Intenta dibujar también los detalles que puedas

A tener en cuenta:

1. Tiene que tener forma de lata, cilíndrica, pero no tiene por qué ser una lata. Se pueden usar herrajes y piezas impresas en 3D.
2. Medidas máximas: 115 mm de alto y 66 mm de diámetro.
3. Le pueden sobresalir las antenas por las partes superior e inferior.
4. Le sobresale el paracaídas también, pero entiendo que por cualquier cara del cilindro.
5. Pesos mínimo-máximo: 300 - 350g.
6. Batería e interruptor general accesibles.
7. Sistema de localización una vez esté en tierra: buzzer o GPS. Quizás luz también.
8. La batería debe durar 4 horas.

Importante: Indica qué materiales usarás en la estructura del dispositivo.

Listado de materiales: ______________________________________________________________________________________________

# 3.- Paracaídas

SITUACIÓN B: Dibuja cómo colocarás el paracaídas en ESTADO DESPLEGADO, después del lanzamiento.

SITUACIÓN A: Dibuja cómo colocarás el paracaídas en ESTADO PLEGADO, antes del lanzamiento. Indica dónde pondremos los anclajes.

Listado de materiales (paracaídas): __________________________________________________________________________________

# 4. Electricidad / electrónica.

## 4.1 Dispositivo de control

Marca una X en el dispositivo de mando (o dispositivos) e indica por qué. Puedes poner el que consideres en las líneas en blanco.

| Modelo | Disponibilidad | Tamaño (mm) | Peso (g) | Alimentación | Voltaje operación
❐ | Arduino UNO | Lo tenemos | 68.6 x 53.4 | 25 | 7 - 12 V | 5 V
❐ | Arduino NANO | Uno. Adquirir más | 18 x 45 | 7 | 7 - 12 V | 5 V
❐ | NodeMCU | Lo tenemos | 58 x 32 x 13 | 8 - 9 | 4.5 - 10 V ¿3.3V? | 3.3 V
❐
❐

Observaciones:

## 4.2 Alimentación

| Modelo | Cantidad >5V | Tamaño Unidad (mm) | Peso Unidad (g) | capacidad | Recargable
❐ | Pilas AA-LR6 | 4 pilas - 6V | 50 x Φ14.2 | ~26g | 2550-3000 mAh | Externamente ¿?
❐ | Pilas AAA-LR03 | 4 pilas - 6V | 44.5 x Φ10.5 | ~12g | 900-1155 mAh | Externamente ¿?
❐ | CR2025 | 2 pilas - 6V | Φ20 × 2,5 | ~2.5g | 170mAh | No
❐ | 18650 | 2 pilas - 3.7V | 65 x Φ18 | ~45g | x2 - 1600 a 3600 mAH | Sí (ver módulos de recarga)
❐
❐

Observaciones:

### Módulos de recarga

TP4056 → módulo de carga con protección para baterías Li-ION.

XL6009 → módulo boost-up de subida de tensión de 3.7V a la necesaria.

Más información en: https://docs.google.com/presentation/d/160dMZFJZibsDr-RB8IfSBjmkvMGqFOZ1Bmg0yL3mbxM/edit?usp=sharing

## 4.3- Sensores y otros

| Modelo | Magnitudes a medir o Función que tenga | Tamaño Unidad (mm) | Peso Unidad (g) | Voltaje de alimentación | Disponible
❐ | bmp180 | Sensor presión barométrica: calcula presión y temperatura , e indirectamente altura. otros bmp280 | 3.6 x 3.8 | ~4g | 3.3 V - 5V | Sí
❐ | DHT11 -DHT22 | Temperatura y humedad | 15.5 x 12 x 5.5 | ~2.7 | 5V | Sí
❐ | GY-521 | MPU6050. Giroscopio y acelerómetro | 21.2 x 16.4 | 2.1 | 3.3V - 5V- Comprobar | Sí
❐ | GY-87 | MPU6050 + HMC5883L + BMP180 → mide aceleración, presión, temperatura, es giroscopio y magnetómetros | 21.80x16.90x02.61 | ~2 | 3.3V - 5V- Comprobar | Sí
❐ | GY-271 | HMC5883L → brújula 3 ejes. | 14.35 x 13.16 x 3.40 | ~2 | 3.3V - 5V- Comprobar | Sí

Observaciones:

## 4.4- Telemetría

Posibles soluciones:

Usar módulo RFM69HC de 868MHz (o 443MHz) . Disponibles. (https://learn.sparkfun.com/tutorials/rfm69hcw-hookup-guide/all)- Módulo emisor con antena ƛ/4 (con dipolo o plano de tierra) y estación de tierra con misma antena receptora o yagi (https://jtecheng.com/?p=957 )

https://youtu.be/fZaSAzRb6YA

https://www.rfwireless-world.com/calculators/3-element-Yagi-Antenna-Calculator.html

Usar los módulos de comunicación NRF24L01, 2.4GHz. ¿necesitaríamos antenas?

## 5- Programación

El lenguaje de programación que creo que debemos usar es el propio del IDE de Arduino, basado en C++. Si crees necesario alguna puntualización en este aspecto, rellena el siguiente apartado:

A4I team Page

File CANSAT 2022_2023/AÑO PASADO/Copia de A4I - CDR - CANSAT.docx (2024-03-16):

CANSAT


Critical DESIGN REVIEW

IES Seritium - A4I

Curso 2021-2022

Índice

Introducción 3

Organización y roles del equipo 3

Objetivos de la misión 3

Descripción del proyecto CANSAT 3

Esquema de la misión 3

Proyecto Científico 3

Diseño de la estructura 4

Paracaídas 4

Diseño eléctrico 5

Software 6

Sistema de recuperación 8

Estación de tierra 8

Planificación del proyecto CANSAT 8

Diagrama de GANTT (cronograma) 8

Presupuesto del CANSAT 9

Apoyo externo 10

Pruebas realizadas 10

Difusión del proyecto 10

Bibliografía / Referencias / Recursos 10

Anexos PROGRAMAS 11

= = = = = = = = = =

# Introducción

¿Construir un satélite e intentar que aterrice y que no se destroce? ¿Que nos envíe datos de la atmósfera? ¿Y ya puestos, por qué no tomar fotos del terreno? ¡Y que nos lo meten en un cohete y todo eso, y nos lo lanzan a un kilómetro de altura, o… dos, o tres…, bueno…, “muy alto”? ¡¡Nos apuntamos!!

## Organización y roles del equipo

1. Adrián Durán Perdigones
2. Iker Espinosa Algeciras
3. Alejandro Chacón Pérez
4. Antonio Jesús Suárez Gómez
5. David García Vázquez y Aurelio Gallardo Rodríguez → profesores

Hemos dedicado 4 horas semanales como si fueran TIC y TIN desde el primer trimestre, y alguna hora más en los recreos y en casa. Alejandro se ha encargado del código, Antonio e Iker de la fabricación de la placa y modelo del Cansat, y Adrián del vídeo y diseños.

## Objetivos de la misión

1. Objetivo 1: Analizar con precisión el clima y terreno.
2. Objetivo 2: Aprender la funcionalidad de un satélite en miniatura.
3. Objetivo 3: Pasarlo bien.

# Descripción del proyecto CANSAT

## Esquema de la misión

Los datos serán recogidos durante el lanzamiento gracias a la telemetría menos las fotos que serán guardadas en una tarjeta SD para no saturar el envío. Esperamos que todos los datos nos lo ofrezcan con la mayor exactitud y al momento; mientras cae haga algunas fotos dependiendo de la altura y obtengamos una análisis completo de todo.

1. Misión primaria: presión, temperatura, altura y telemetría.
2. Misión secundaria: lo demás, GPS, acelerómetro y toma de fotos.

## Proyecto Científico

La fotografía aérea tiene múltiples aplicaciones: topografía/cartografía, análisis de cultivos o masas forestales, aspectos geológicos, hidrológicos, análisis de la actividad humana y prevención de riesgos, e incluso análisis arqueológicos.

Usamos el GPS para saber dónde está el Cansat al caer, las fotos para analizar campos de cultivos o un terreno; presión, temperatura y altura para analizar el clima y realice una función de satélite; el acelerómetro para calcular la velocidad a la que se encuentra el Cansat y su posible orientación, y la telemetría para que nos llegue los datos en vivo.

## Diseño de la estructura

Planos de la estructura. En vertical, pieza donde se alojan las pilas (habitáculo pilas), la antena emisora, el módulo GPS y ranura y anclaje de la placa electrónica. En horizontal, resto de piezas y perspectiva general.

Leyenda: Lateral A (1) , Lateral B (2), Base antena - ground (3), Agujeros cordajes paracaídas (4), Tapa habitáculo pilas (5), ranura placa electrónica (6), agujeros pasantes para varillas roscadas de la estructura (7) y (8), Superficie donde irá la cámara (9), Separador (10).


### Paracaídas

Cordaje: tanza 80LB (36.3Kgf). Tensión máxima que soporta.

Tela paracaídas: taffta nylon. 70D (unidades deniers) y entre 190/210T (trenzado de líneas horizontales/verticales). Tela especial para paracaídas y tiendas de campaña: ver bibliografía.

## Diseño eléctrico

Más cosas que decir:

-Baterías.

-Módulo de carga.

-Placa hecha artesanal

-Componentes usados normalmente encontrados y no comprados.

Consumo teórico de componentes importantes:

- Arduino Pro Mini: 200mA máximo en el chip
- ESP32 CAM: 180mA sin flash
- GY-87 (Acelerómetro): MPU6050 → 10 mA máximo. BMP180 → 1mA pico
- LORA 868MHz: 130mA máximo transmitiendo
- NEO6 GPS: 45mA
- LED: menos de 70mA

IT teórico < 636mA

Consumo total de la placa en funcionamiento: IT = 220 mA max, medido con amperímetro, con LED encendido.

Carga de las pilas (tantalato litio): Q = I⋅t = 3000mAh ⋅2= 6000 mAh (). Con pilas estándar 18650, Q = I⋅t = 2200mAh ⋅2= 4400 mAh

Tiempo de encendido teórico: t > Q/I = 4400mAh/636mA = 6.9h y t > Q/I = 6000mAh/636mA = 9.4h con pilas estándar y tantalato de litio, respectivamente.

Tiempo de encendido práctico: t > Q/I = 4400mAh/ 200 mA = 22h y t > Q/I =6000mAh/ 200mA =60h

Enlaces a componentes; intensidades máximas teóricas:

-Arduino: https://components101.com/microcontrollers/arduino-pro-mini

-Módulo Lora:https://learn.sparkfun.com/tutorials/rfm69hcw-hookup-guide/all

-GY-87: MPU6050 → 10 mA máximo (https://www.elecrow.com/crowtail-mpu6050-accelerometer-gyro.html)

BMP180 → 1mA pico (https://components101.com/sensors/bmp180-atmospheric-pressure-sensor)

-ESP32 cam:https://loboris.eu/ESP32/ESP32-CAM%20Product%20Specification.pdf

-NEO6 GPS:https://lastminuteengineers.com/neo6m-gps-arduino-tutorial/

-Baterías:https://es.aliexpress.com/item/32835795441.html?gatewayAdapt=glo2esp&spm=a2g0o.order_list.0.0.21ef194dWV3ghg

Esquemático eléctrico / electrónico



Pistas cobre | Serigrafía superior / puentes

## Sistema de recuperación

La idea es que al caer sepamos donde está mediante los datos de GPS, y cuando estemos cerca podamos ver la luz parpadeando ya que el GPS no da información tan exacta.

## Telemetría

El cansat tras recopilar los datos los envía al módulo lora el cual modula la señal a 868mHz y los envía por la antena.

## Estación de tierra

La estación de tierra está compuesta por un nodemcu como procesador, un módulo lora receptor y la propia antena yagi fabricada por nosotros en el taller. Esta estación recibe los datos por la antena yagi, las pasa al módulo lora la cual lo demodula y la muestra en la pantalla del ordenador por el puerto serie.

## Software

Hemos usado arduino como entorno de desarrollo, programando con su IDE oficial.

Para enviar a tierra los datos, los encriptamos y los enviamos mediante el módulo RFM69 a la estación de tierra. Los datos recopilados son divididos en 2 grupos,que se envían en dos cadenas distintas: La primera, con datos de aceleración y giros en los 3 ejes, presión (Y, derivada de esta, la altitud del CanSat), y temperatura; y la segunda, con datos de posicionamiento GPS y informe sobre si se ha tomado foto o no.

Diagrama de flujo


Estructura de datos

Seguir el enlace: https://docs.google.com/spreadsheets/d/1UBlOgZCoYUfe1Wo4PusJnSwNe_fxC9IOaQ9bJyCvJZQ/edit?usp=sharing


Se envían dos cadenas alternas. Descripción informaciones:

1. Código de cadena, código del centro, temperatura ºC, presión PA, 10xaltura m, 10xAx, 10xAy, 10xAz (m/s2), 10xangX, 10xangY, 10xangZ (º)
2. Código de cadena, código del centro,latitud, longitud, Si se ha tomado o no foto.

# Planificación del proyecto CANSAT

## Diagrama de GANTT (cronograma)


## Presupuesto del CANSAT

(*) Estación de tierra.

Concepto | Valor / Observaciones | Cantidad | Precio (€)
Led | Para señalización | 1 | 0,01 €
Buzzer activo | | 1 | 0,1 €
Interruptor | Mini para placa | 1 | 0,01 €
Resistencia | | 1 | 0,01 €
Cond. electrolítico | 47uF | 1+1(*) | 0,02 €
NodeMCU V2 | ESP8266 | 1 (*) | 3 €
Arduino pro mini | Logic 3.3V | 1 | 5 €
ESP32-CAM | Con cámara OV2640 75 mm 2MP | 1 | 6€ + 3,5€ = 9,5€
LORA 868MHz | | 1 + 1(*) | 3€
GY-87 | acelerómetro + giroscopio + presión + temperatura | 1 | 5,5€
NEO6 GPS | | 1 | 4€
Piezas 3D 45g al 25% densidad + 56g al 50% = 101g | Habitáculo pilas (56g/50%) | 1 | PLA Amarillo 1 Kg a ~17€ ~1,7€
| Separador | 2
| Tapa habitáculo pilas | 1
| Lateral A (Antena) | 1
| Lateral B | 1
Tornillería, cableado, conectores. Estaño. | Disponibles en el taller | ? | 1€
Antena emisora y receptora, para CANSAT y estación tierra | Construidas con materiales del taller: arandelas y alma de cobre de cables de D1.5 | 2 | 2 x 0,5€ = 1 €
Placa electrónica 41 x 104 mm | 70 x 100 mm | 1 | 1 €
Pilas 18650 | Tantalato de litio | 2 | 15,4€/ 2 = 7,7 €
Módulo de carga | Equivalente TP4056 | 1 | 0,5€
Tarjeta microSD | 32GB | 1 | 3€
Tela paracaídas | | 1 | 2,74 € x 1,5m2
Tanza pesca 4 hebras | | 1 | 5,5€
TOTAL: | | | 55,29€

## Apoyo externo

En principio, hemos contado con recursos propios y material suministrado por los profesores.

## Pruebas realizadas

En el enlace: https://www.seritium.es/wordpress/index.php/2022/03/24/proyecto-cansat-2022/

# Difusión del proyecto

1. Página web: www.seritium.es
2. Facebook: https://www.facebook.com/ies.seritium.jerez
3. Twitter: @IesSeritium

# Bibliografía / Referencias / Recursos

1. Modelización del paracaídas: https://www.translatorscafe.com/unit-converter/es-ES/calculator/parachute-size/
2. Cordaje paracaídas: https://es.aliexpress.com/item/1549494151.html?gatewayAdapt=glo2esp&spm=a2g0o.order_list.0.0.21ef194dWV3ghg
3. GY-87: https://www.luisllamas.es/arduino-orientacion-imu-mpu-6050/ , https://electropeak.com/learn/interfacing-gy-87-10dof-imu-mpu6050-hmc5883l-bmp085-module-with-arduino/, https://naylampmechatronics.com/blog/45_tutorial-mpu6050-acelerometro-y-giroscopio.html
4. ESP32-CAM: https://randomnerdtutorials.com/esp32-cam-video-streaming-face-recognition-arduino-ide/
5. Telemetría: https://learn.sparkfun.com/tutorials/rfm69hcw-hookup-guide/all, https://iot.uy/conectar-la-radio-rfm69-hcw-al-esp8266/, https://www.openhardware.io/view/171/Connecting-the-Radio, https://learn.adafruit.com/adafruit-rfm69hcw-and-rfm96-rfm95-rfm98-lora-packet-padio-breakouts/overview, https://forum.arduino.cc/t/nodemcu-and-rfm69hw-s2/599219/16
6. GPS: https://www.luisllamas.es/localizacion-gps-con-arduino-y-los-modulos-gps-neo-6/
7. Antena Yagi: https://www.changpuak.ch/electronics/yagi_uda_antenna_DL6WU.php

# Anexos PROGRAMAS

Programas en el emisor (satélite CANSAT)

/*** CanSat Unificado ***/

/* Programa unificado para el proyecto CanSat 2021/2022

* Dispositivo: Arduino Pro Mini (3.3v)

* Fecha: 8/1/2022

*/

/* -=- Por hacer -=-

* - Cámara así? Más pruebas?

*/

/* -=- Changelog -=-

* - 31/03/2022: Añadida la lectura de giro en el eje z. Añadido el envío de altura para la cámara. Limpieza de código.

* - 11/04/2022: Eliminada la función de envio de datos a la cámara. Por ahora lo dejamos así.

*/

/* -=- PINOUT -=-

* RX -----------3

* TX -----------4

* SDA ----------A4

* SCL ----------A5

* MOSI----------11

* MISO ---------12

* SCK ----------13

* NSS ----------10

* DIO0----------2

* ESP32-CAM-----6

*/

#include <RFM69.h>

#include <SPI.h>

#include <Adafruit_BMP085.h>

#include "I2Cdev.h"

#include "MPU6050.h"

#include "Wire.h"

#include <SoftwareSerial.h>

// Addresses for this node. CHANGE THESE FOR EACH NODE!

#define NETWORKID 100 // Must be the same for all nodes --> esta es la red.

#define MYNODEID 10 // My node ID --> este es el nodo de mi dispositivo

#define TONODEID 20 // Destination node ID --> este es el nodo del otro dispositivo

#define FREQUENCY RF69_868MHZ

#define FREQUENCY_E 868001000UL // frecuencia exacta

// AES encryption (or not):

#define ENCRYPT true // Set to "true" to use encryption

#define ENCRYPTKEY "123456789" // Use the same 16-byte key on all nodes --> clave secreta

// Use ACKnowledge when sending messages (or not):

#define USEACK false // Request ACKs or not

// Según la web https://iot.uy/conectar-la-radio-rfm69-hcw-al-esp8266/

#define SPI_CS 10 //NSS

#define IRQ_PIN 2 // DIO0

#define IRQ_NUM 2 //IRQ igual al pin

#define IS_RFM69HCW true // Si tu radio es RFM69HCW entonces va "true"

#define POWER_LEVEL 31 // Valor máximo de potencia

// -=- OBJETOS -=-

RFM69 radio = RFM69(SPI_CS, IRQ_PIN, IS_RFM69HCW, IRQ_NUM);

MPU6050 sensor; // Iniciamos sensor mpu6050

Adafruit_BMP085 bmp; // Iniciamos el BMP180

SoftwareSerial gps (3, 4); // Iniciamos el GPS (rxPIN, txPIN)

//SoftwareSerial cam(7, 6); // Iniciamos la comunicación con la cámara (Chequear pines)

const int led = 5;

// -=- DATOS A REGISTRAR -=-

// Cadena del GPS --> $GPRMC,225446,A,4916.45,N,12311.12,W,000.5,054.7,191194,020.3,E*68

String cadenaGPS = ""; // Cadena GPS

const unsigned int codigoSeritium = 11700767; // Código del centro

float temperatura = -99.9; // Ejemplo de temperatura con signo (2 dígitos + 1 decimal)

unsigned int presion = 999999; // Ejemplo de presión atmosférica. Entero positivo sin decimales.

float altura = 9999.9; // Ejemplo de altura. Positivo sin signo (4 dígitos + 1 decimal)

float alturaPrev = 9999.9;

float ace[3] = {+39.2,-39.2,+39.2}; // valores entre -4g y 4g, en m/s2. Con signo (2 dígitos + 1 decimal)

float ang[3] = {-90.0,+90.0,-45.5}; // valores entre -90 y 90, en grados. Con signo (2 dígitos + 1 decimal)

bool foto = false; // Si el programa ha tomado o no fotografías.

// -=- DATOS DEL GIRSOCOPIO -=-

short int ax, ay, az;

short int gx, gy, gz; // Valores sin procesar del acelarómetro y giroscopio.

long p0; // Valor de la presión inicial.

long tiempo_prev;

float dt; // Variables que calculan el tiempo (Cálculos aceleromtro/giroscopio)

float ang_x, ang_y, ang_z;

float ang_x_prev, ang_y_prev, ang_z_prev; // Variables para calcular los ángulos relativos de rotación.

//-=- Variables para el LED

unsigned long t = 0;

// ======================

// SETUP

// ======================

void setup() {

delay(2000);

pinMode(led, OUTPUT);

Serial.begin(9600);

Serial.print("Node ");

Serial.print(MYNODEID,DEC);

Serial.println(" ready");

Wire.begin();

gps.begin(9600);

//cam.begin(115200);

sensor.initialize();

if(sensor.testConnection()){

Serial.println("Sensor MPU6050 iniciado correctamente");

}

else{

Serial.println("Error al iniciar el sensor MPU6050");

}

if(!bmp.begin()){

Serial.print("Error al iniciar el sensor BMP180");

}

else{

Serial.println("Sensor BMP180 iniciado correctamente");

} //Inicializamos comunicación Serial y ambos sensores.

p0 = bmp.readPressure();

Serial.print("Presión inicial = ");

Serial.println(p0);

Serial.println("------------------------------------------"); //Tomamos la presión inical, que usaremos para calcular la altura.

radio.initialize(FREQUENCY, MYNODEID, NETWORKID);

radio.setHighPower(); // Always use this for RFM69HCW

// afinar frecuencia

radio.setFrequency(FREQUENCY_E);

// Saber más en: https://www.aprendiendoarduino.com/tag/banda-ism/

// rango de 863 a 870 MHz

// Turn on encryption if desired:

if (ENCRYPT) {

radio.encrypt(ENCRYPTKEY); }

Serial.println("Terminado SETUP...");

}

// ======================

// LOOP

// ======================

void loop() {

leerGY87();

extraerCadenaGPS();

delay(800); // Cada 500 milisegundos

enviarDatos(cadenaParaEnviar(1)); // Primero llama a la funcion cadenaParaEnviar con valor 1,

// que formatea los datos de temperatura, presión, altura, aceleración, ángulos.

// Los concatena en una cadena que empieza por @ y termina por #. Tamaño máximo 61 caracteres.

// Al principio incluye un 0, primer dato, y separado por ? el código del centro IES Seritium,

// Posteriormente, separado por ?, el resto de los datos. Acaba con #

delay(800); // cada 500 milisegundos

enviarDatos(cadenaParaEnviar(2)); // Idem caso anterior pero con valor 2.

// envía la latitud, la longitud y si se ha sacado o no foto.

t = millis();

digitalWrite(led, ((t/2500)%2)*((t/200)%2)*(altura<= 100)); //Hace parpadear al LED 2 veces cada 10 segundos.

//if(((int(altura) /*% 10*/) == 0)/* and (altura =! alturaPrev) and (altura >30)*/){ //Envio de datos de altura a la cámara.

/*if((t % 20000) == 0){

cam.print(0);

cam.flush();

alturaPrev = altura;

}*/

digitalWrite(6, LOW);

}

// ======================

// Funciones

// ======================

// ********************************

// Enviando cadena

// ********************************

void enviarDatos(String datos) {

// Envío de datos

static char sendbuffer[62];

static int sendlength = 0;

sendlength = datos.length();

datos.toCharArray(sendbuffer,sendlength);

Serial.println(datos);

if (USEACK){

if (radio.sendWithRetry(TONODEID, sendbuffer, sendlength))

Serial.println("ACK received!");

else

Serial.println("no ACK received");

}

// If you don't need acknowledgements, just use send():

else // don't use ACK

{

radio.send(TONODEID, sendbuffer, sendlength);

Serial.println("Enviado...");

}

sendlength=0;

}

void leerGY87(){

sensor.getAcceleration(&ax, &ay, &az);

sensor.getRotation(&gx, &gy, &gz); //Obtenemos las lecturas de aceleración y girsocopio.

dt = (millis()-tiempo_prev)/1000.0;

tiempo_prev = millis(); //Calculamos el tiempo pasado entre cada medición.

float ang_x_accel = atan(ax/sqrt(pow(ay,2) + pow(az,2)))*(180.0/3.14);

float ang_y_accel = atan(ay/sqrt(pow(az,2) + pow(ax,2)))*(180.0/3.14);

float ang_z_accel = atan(az/sqrt(pow(ax,2) + pow(ay,2)))*(180.0/3.14); //Calculamos los angulos de inclinación en los ejes usando el acelerómetro.

ang_x = 0.98*(ang_x_prev+(gx/131)*dt) + 0.02*ang_x_accel;

ang_y = 0.98*(ang_y_prev+(gy/131)*dt) + 0.02*ang_y_accel;

ang_z = 0.98*(ang_z_prev+(gy/131)*dt) + 0.02*ang_z_accel; //Calculamos la rotación usando tanto el girsocopio como el acelerómetro para eliminar errores.

ang_x_prev = ang_x;

ang_y_prev = ang_y;

ang_z_prev = ang_z;

ace[2] = az * (9.81/16384.0);

ace[1] = ay * (9.81/16384.0);

ace[0] = ax * (9.81/16384.0); //Calculamos la aceleración en m/s2 en los tres ejes

ang[0] = ang_x_accel;

ang[1] = ang_y_accel;

ang[2] = ang_z_accel;

altura = bmp.readAltitude(p0);

presion = bmp.readPressure();

//float m_az_ax = sqrt(pow(sqrt((pow(ax_ms2, 2)) + (pow(az_ms2, 2))), 2) + (pow(ay_ms2, 2))); //Calculamos el módulo de los 3 vectores, para así obtener la aceleración que experimenta.--> NO SE USA POR AHORA.

Serial.print("Rotación en X: ");

Serial.print(ang[0]);

Serial.print("º\tRotación en Y: ");

Serial.print(ang[1]);

Serial.print("º \tAceleración de caída(m/s2): ");

Serial.print(ace[2]);

Serial.print("\tTemperatura = ");

temperatura = bmp.readTemperature();

Serial.print(temperatura);

Serial.print("ºC\tPresión = ");

Serial.print(presion);

Serial.print("\tAltitud respecto al suelo = ");

Serial.print(altura);

Serial.println("m"); //Mostramos por puerto serie los datos obtenidos.

}

void extraerCadenaGPS(){

if(gps.available()){

String cadenaFinal = gps.readStringUntil('\n'); //Leemos lo que nos ha llegado hasta el salto de línea.

if (cadenaFinal.startsWith("$GPRMC")) {

int pos = cadenaFinal.indexOf("$GPRMC"); //Si empieza por el código que queremos, pillamos la posición de inicio.

if (pos == 0) {

cadenaGPS = cadenaFinal;

Serial.println(cadenaFinal); //Si la posición es 1, significa que tenemos toda la cadena, así que la recortamos y la imprimimos.

}

}

}

}

// ********************************

// cadena ya formateada para enviar

// ********************************

String cadenaParaEnviar (int cual) {

char tmp[62]; // variable de 62 bytes, del 0 al 61

switch (cual) {

// en este caso formateo los datos de temperatura, presión, altura, aceleración, ángulos.

case 1:

sprintf(tmp,"@%1d?%8d?%1d%3d?%6d?%5d?%1d%3d?%1d%3d?%1d%3d?%1d%3d?%1d%3d?%1d%3d?#",cual,codigoSeritium

,(temperatura>=0),(int) (abs(temperatura*10))

,presion,(int) (altura*10)

,(ace[0]>=0), (int) abs(ace[0]*10),(ace[1]>=0), (int) abs(ace[1]*10),(ace[2]>=0), (int) abs(ace[2]*10)

,(ang[0]>=0), (int) abs(ang[0]*10),(ang[1]>=0), (int) abs(ang[1]*10),(ang[2]>=0), (int) abs(ang[2]*10) );

break;

// en este caso envío los datos de latitud, longitud y si se ha sacado una foto

case 2:

sprintf(tmp,"@%1d?%8d?%6d%1s?%7d%1s?%1d?#",cual,codigoSeritium

,(int) ( 100.0 * parte(cadenaGPS,',',3).toFloat() ), parte(cadenaGPS,',',4)

,(int) ( 100.0 * parte(cadenaGPS,',',5).toFloat() ), parte(cadenaGPS,',',6)

,(int) foto);

// Serial.println(parte(cadenaGPS,',',0)); // importante usar simple quotas ' ' ' '

break;

// por defecto

default:

break;

}

return tmp; // devuelve el conjunto de caracteres

}

// ********************************

// encuentra parte de una cadena

// ********************************

String parte(String data, char separator, int index)

{

int found = 0;

int strIndex[] = {0, -1};

int maxIndex = data.length()-1;

for(int i=0; i<=maxIndex && found<=index; i++){

if(data.charAt(i)==separator || i==maxIndex){

found++;

strIndex[0] = strIndex[1]+1;

strIndex[1] = (i == maxIndex) ? i+1 : i;

}

}

return found>index ? data.substring(strIndex[0], strIndex[1]) : "";

}

===============================================

Programa en el receptor (estación TIERRA)

/*

* Ejemplo de envío de datos por telemetría

* Dispositivo: NodeMCU con valores lógicos a 3.3V

* Fecha: 8/1/2022

*/

// Include the RFM69 and SPI libraries:

#include <RFM69.h>

#include <SPI.h>

// Addresses for this node. CHANGE THESE FOR EACH NODE!

#define NETWORKID 100 // Must be the same for all nodes --> esta es la red.

#define MYNODEID 20 // My node ID --> este es el nodo de mi dispositivo

#define TONODEID 10 // Destination node ID --> este es el nodo del otro dispositivo

// RFM69 frequency, uncomment the frequency of your module:

//#define FREQUENCY RF69_433MHZ

// #define FREQUENCY RF69_915MHZ

#define FREQUENCY RF69_868MHZ

#define FREQUENCY_E 868001000UL // frecuencia exacta

// AES encryption (or not):

#define ENCRYPT true // Set to "true" to use encryption

#define ENCRYPTKEY "123456789" // Use the same 16-byte key on all nodes --> clave secreta

// Use ACKnowledge when sending messages (or not):

#define USEACK false // Request ACKs or not

// Packet sent/received indicator LED (optional):

// #define LED 9 // LED positive pin

// #define GND 8 // LED ground pin

// Según la web https://iot.uy/conectar-la-radio-rfm69-hcw-al-esp8266/

#define SPI_CS D8 //NSS o Cable Select al GPIO15 o D8

#define IRQ_PIN D1 // DIO0 conectado a GPIO4

#define IRQ_NUM D1 //IRQ igual al pin

#define IS_RFM69HCW true // Si tu radio es RFM69HCW entonces va "true"

#define POWER_LEVEL 31 // Valor máximo de potencia

// Create a library object for our RFM69HCW module:

RFM69 radio = RFM69(SPI_CS, IRQ_PIN, IS_RFM69HCW, IRQ_NUM);

// Datos que deben ser registrados

// GPS -->

String latitud ="";

String longitud="";

// Valores

unsigned int codigoSeritium = 0; // Código del centro

float temperatura = 0.0; // Ejemplo de temperatura con signo (2 dígitos + 1 decimal)

unsigned int presion = 0; // Ejemplo de presión atmosférica. Entero positivo sin decimales.

float altura = 0.0; // Ejemplo de altura. Positivo sin signo (4 dígitos + 1 decimal)

float ace[3] = {0.0, 0.0, 0.0}; // valores entre -4g y 4g, en m/s2. Con signo (2 dígitos + 1 decimal)

float ang[3] = {0.0, 0.0, 0.0}; // valores entre -90 y 90, en grados. Con signo (2 dígitos + 1 decimal)

bool foto = false; // Si el programa ha tomado o no fotografías.

// potencia recibida

int potencia = 0;

// ======================

// SETUP

// ======================

void setup() {

delay(2000);

Serial.begin(9600);

Serial.print("Node ");

Serial.print(MYNODEID,DEC);

Serial.println(" ready");

// Initialize the RFM69HCW:

// radio.setCS(10); //uncomment this if using Pro Micro

radio.initialize(FREQUENCY, MYNODEID, NETWORKID);

radio.setHighPower(); // Always use this for RFM69HCW

// afinar frecuencia

radio.setFrequency(FREQUENCY_E);

// Saber más en: https://www.aprendiendoarduino.com/tag/banda-ism/

// rango de 863 a 870 MHz

// Turn on encryption if desired:

if (ENCRYPT) {

radio.encrypt(ENCRYPTKEY); }

Serial.println("Terminado SETUP...");

}

// ======================

// LOOP

// ======================

void loop() {

delay(100); // tiene que ser más rápido que el envío de datos... Si se envían cada 500 ms, por ejemplo,

// aquí ponemos la mitad o así...

String cadena = recibirDatos();

if (cadena.length()>2) {analizaCadena(cadena); } // lama a la función que empieza a leer los datos.

} // Fin del LOOP

// ======================

// Funciones

// ======================

// ********************************

// Recibiendo cadena

// ********************************

String recibirDatos() {

char temp[63]; // un byte más de lo necesario

// String tmp;

if (radio.receiveDone()) // Got one!

{

// Print out the information:

// Serial.println( (int) radio.DATALEN);

// Serial.println(radio.DATA);

// The actual message is contained in the DATA array,

// and is DATALEN bytes in size:

for (byte i = 0; i < radio.DATALEN; i++) {

char n = (char)radio.DATA[i];

if (n=='#') {

temp[i]=NULL ; break;

} else if (n=='@') {

temp[i]='?';

} else {

temp[i]= n;

}

// Serial.print((char)radio.DATA[i]);

// Serial.print(temp[i]);

// tmp.concat(temp[i]);

}

// int bufferLength = sizeof(temp);

// Serial.println("Tamaño del buffer: " + (String) bufferLength);

// Serial.print("received from node ");

// Serial.print(radio.SENDERID, DEC);

// Serial.print(", message [");

// for (int j=0; j<bufferLength; j++) {

// Serial.print(temp[j]);

// }

// RSSI is the "Receive Signal Strength Indicator",

// smaller numbers mean higher power.

// Serial.print("], RSSI ");

// Serial.println(radio.RSSI);

potencia = (int) radio.RSSI;

// Send an ACK if requested.

// (You don't need this code if you're not using ACKs.)

if (radio.ACKRequested())

{

radio.sendACK();

Serial.println("ACK sent");

}

}

return String(temp);

// return tmp;

}

// ********************************

// análisis de cadena

// ********************************

void analizaCadena (String trama) {

String d; // dato que recibe

String comodin; // cadena comodin

d = parte(trama,'?',1); // debe recibir o un 1 o un 2

codigoSeritium = parte(trama,'?',2).toInt();

switch (d.toInt()) {

// recibo la primera cadena

case 1:

Serial.println("Potencia: " + (String) potencia + " // Cadena 1 --> " + trama);

Serial.println("Recibido para el centro: "+ (String) codigoSeritium);

// Temperatura

temperatura = recValorFloat (parte(trama,'?',3), 10, true); // cadena a recuperar, divisor, si tiene signo

// Presión

comodin = parte(trama,'?',4);

presion = comodin.toInt();

// Altura

altura = recValorFloat (parte(trama,'?',5), 10, false);

// Aceleracion

comodin ="Aceleraciones: ";

for (int i=0;i<3;i++) {

ace[i]=recValorFloat (parte(trama,'?',i+6), 10, true); // valores 6, 7 y 8

comodin = comodin + "A"+char(120+i)+" = "+ace[i]+" m/s2 ~ ";

}

comodin = comodin.substring(0,comodin.length()-2);

// Ángulos

comodin = comodin + "\nÁngulos: ";

for (int i=0;i<3;i++) {

ang[i]=recValorFloat (parte(trama,'?',i+9), 10, true); // valores 9, 10 y 11

comodin = comodin + "ANG"+char(120+i)+" = "+ang[i]+" º ~ ";

}

comodin = comodin.substring(0,comodin.length()-2);

// Muestra los datos en el monitor serie

Serial.println("T = "+(String) temperatura +" º C // "+

"P = "+(String) presion +" Pa // "+

"h = "+(String) altura +" m // ");

Serial.println(comodin);

break;

// ************************************************

// recibo la segunda cadena

case 2:

Serial.println("Potencia: " + (String) potencia + " // Cadena 2 --> " + trama);

Serial.println("Recibido para el centro: "+ (String) codigoSeritium);

// latitud

comodin = parte(trama,'?',3);

latitud = comodin.substring(0,2)+"º "+(String) recValorFloat(comodin.substring(2,6), 100, false)

+"' "+ cambioLetra(comodin.substring(6,7));

// longitud

comodin = parte(trama,'?',4);

longitud = comodin.substring(0,3)+"º "+(String) recValorFloat(comodin.substring(3,7), 100, false)

+"' "+ cambioLetra(comodin.substring(7,8));

// Fotografía

comodin = parte(trama,'?',5);

foto = (comodin=="1");

comodin = (foto) ? "Sí" : "No";

Serial.println("LAT: "+latitud+ " // LON: "+longitud);

Serial.println("¿Se ha tomado una foto?: "+ comodin);

break;

// *******************************************

default:

// Serial.println("No he encontrado una cadena: " + trama);

return; // sale de la función

break;

}

// imprime línea de caracteres

int iguales = 91;

while (--iguales) { Serial.print("="); }

Serial.print("\n");

}

// ********************************

// Recupera valores float

// ********************************

float recValorFloat (String num, int divisor, bool signo) {

float valor = 0.0;

int longitud = num.length();

if (signo) {

valor = num.substring(1,longitud).toFloat()/divisor;

valor = (num.substring(0,1)=="0") ? valor = -1*valor : valor;

} else {

valor = num.toFloat()/divisor;

}

return valor;

}

// ********************************

// cambio letra en longitud

// ********************************

String cambioLetra (String letra) {

return (letra=="W") ? "Oeste" : (letra=="E") ? "Este" : (letra=="N") ? "Norte" : (letra=="S") ? "Sur" : "" ;

}

// ********************************

// encuentra parte de una cadena

// ********************************

String parte(String data, char separator, int index)

{

int found = 0;

int strIndex[] = {0, -1};

int maxIndex = data.length()-1;

for(int i=0; i<=maxIndex && found<=index; i++){

if(data.charAt(i)==separator || i==maxIndex){

found++;

strIndex[0] = strIndex[1]+1;

strIndex[1] = (i == maxIndex) ? i+1 : i;

}

}

return found>index ? data.substring(strIndex[0], strIndex[1]) : "";

}

===============================================

Programa en el ESP32-CAM

#include "esp_camera.h"

#include "Arduino.h"

#include "FS.h" // SD Card ESP32

#include "SD_MMC.h" // SD Card ESP32

#include "soc/soc.h" // Disable brownour problems

#include "soc/rtc_cntl_reg.h" // Disable brownour problems

#include "driver/rtc_io.h"

#include <EEPROM.h> // read and write from flash memory

// define the number of bytes you want to access

#define EEPROM_SIZE 1

// Pin definition for CAMERA_MODEL_AI_THINKER

#define PWDN_GPIO_NUM 32

#define RESET_GPIO_NUM -1

#define XCLK_GPIO_NUM 0

#define SIOD_GPIO_NUM 26

#define SIOC_GPIO_NUM 27

#define Y9_GPIO_NUM 35

#define Y8_GPIO_NUM 34

#define Y7_GPIO_NUM 39

#define Y6_GPIO_NUM 36

#define Y5_GPIO_NUM 21

#define Y4_GPIO_NUM 19

#define Y3_GPIO_NUM 18

#define Y2_GPIO_NUM 5

#define VSYNC_GPIO_NUM 25

#define HREF_GPIO_NUM 23

#define PCLK_GPIO_NUM 22

int pictureNumber = 0;

void setup() {

WRITE_PERI_REG(RTC_CNTL_BROWN_OUT_REG, 0); //disable brownout detector

Serial.begin(115200);

pinMode(4, OUTPUT);

//Serial.setDebugOutput(true);

//Serial.println();

camera_config_t config;

config.ledc_channel = LEDC_CHANNEL_0;

config.ledc_timer = LEDC_TIMER_0;

config.pin_d0 = Y2_GPIO_NUM;

config.pin_d1 = Y3_GPIO_NUM;

config.pin_d2 = Y4_GPIO_NUM;

config.pin_d3 = Y5_GPIO_NUM;

config.pin_d4 = Y6_GPIO_NUM;

config.pin_d5 = Y7_GPIO_NUM;

config.pin_d6 = Y8_GPIO_NUM;

config.pin_d7 = Y9_GPIO_NUM;

config.pin_xclk = XCLK_GPIO_NUM;

config.pin_pclk = PCLK_GPIO_NUM;

config.pin_vsync = VSYNC_GPIO_NUM;

config.pin_href = HREF_GPIO_NUM;

config.pin_sscb_sda = SIOD_GPIO_NUM;

config.pin_sscb_scl = SIOC_GPIO_NUM;

config.pin_pwdn = PWDN_GPIO_NUM;

config.pin_reset = RESET_GPIO_NUM;

config.xclk_freq_hz = 20000000;

config.pixel_format = PIXFORMAT_JPEG;

if(psramFound()){

config.frame_size = FRAMESIZE_UXGA; // FRAMESIZE_ + QVGA|CIF|VGA|SVGA|XGA|SXGA|UXGA

config.jpeg_quality = 10;

config.fb_count = 2;

} else {

config.frame_size = FRAMESIZE_SVGA;

config.jpeg_quality = 12;

config.fb_count = 1;

}

// Init Camera

esp_err_t err = esp_camera_init(&config);

if (err != ESP_OK) {

Serial.printf("Camera init failed with error 0x%x", err);

return;

}

//Serial.println("Starting SD Card");

if(!SD_MMC.begin()){

Serial.println("SD Card Mount Failed");

return;

}

uint8_t cardType = SD_MMC.cardType();

if(cardType == CARD_NONE){

Serial.println("No SD Card attached");

return;

}

}

void loop() {

int t = millis();

if((t%10000) == 0){

camera_fb_t * fb = NULL; // Take Picture with Camera

fb = esp_camera_fb_get();

if(!fb) {

Serial.println("Camera capture failed");

return;

}

// initialize EEPROM with predefined size

//EEPROM.begin(EEPROM_SIZE);

//pictureNumber = EEPROM.read(0) + 1;

pictureNumber = t/10000;

// Path where new picture will be saved in SD Card

String path = "/picture" + String(pictureNumber) +".jpg";

fs::FS &fs = SD_MMC;

Serial.printf("Picture file name: %s\n", path.c_str());

File file = fs.open(path.c_str(), FILE_WRITE);

if(!file){

Serial.println("Failed to open file in writing mode");

}

else {

file.write(fb->buf, fb->len); // payload (image), payload length

Serial.printf("Saved file to path: %s\n", path.c_str());

//EEPROM.write(0, pictureNumber);

//EEPROM.commit();

}

file.close();

esp_camera_fb_return(fb);

// Turns off the ESP32-CAM white on-board LED (flash) connected to GPIO 4

digitalWrite(4, LOW);

}

}

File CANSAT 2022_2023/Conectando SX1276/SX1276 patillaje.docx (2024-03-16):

parece mejor explicado en

https://how2electronics.com/lora-sx1278-esp8266-transmitter-receiver/

Parece que el transmisor no necesita ni RST ni DIO0, pero el receptor sí.


https://circuitdigest.com/microcontroller-projects/esp32-lora-communication-with-the-things-network

De aquí saco el patillaje. cambia en uno respecto al año anterior. Aunque parece que el módulo SX1276 equivale al RFM95W


https://www.researchgate.net/publication/361916974_Designing_a_Double_LoRa_Connectivity_for_the_Arduino_Portenta_H7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


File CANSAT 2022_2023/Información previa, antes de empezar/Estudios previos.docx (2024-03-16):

https://forum.arduino.cc/t/real-time-clock/590501/2

# Sobre medición de tiempo y arduino/ESP32

1. https://www.instructables.com/625-Nanosecond-Resolution-Timer-for-Any-Microcontr/
2. https://github.com/OliviliK/ESP32_timer_u32
3. https://electronics.stackexchange.com/questions/549224/how-do-i-make-a-nanoseconds-counter
4. Señal DCF77 → https://hmong.es/wiki/DCF77 ¿¿??
5. https://www.ti.com/lit/ds/symlink/tdc7200.pdf

# Sobre potencia de señal recibida y cálculo de distancias

1. https://www.researchgate.net/figure/LoRa-range-measurement-vs-RSSI-To-estimate-the-next-position-of-a-mobile-device-we_fig1_334627867
2. https://www.rs-online.com/designspark/lora-location-tracker-rssi
3. https://youtu.be/C4QYCReGEUY
4. https://upcommons.upc.edu/bitstream/handle/2117/347444/A_minimalistic_distance_vector_routing_protocol_for_LoRa_mesh_networks.pdf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

# Sobre geolocalización usando GSM y antenas móviles

1. https://programarfacil.com/podcast/gps-arduino-geolocalizacion/
2. GSM: sim800 →
3. Mapa de estaciones de telefonía móvil → https://geoportal.minetur.gob.es/VCTEL/vcne.do y https://antenasgsm.com/

# Sobre funcionamiento del GPS y trilateración o triangulación

1. https://youtu.be/4O3ZVHVFhes
2. https://www.youtube.com/watch?v=8eTlI19_57g

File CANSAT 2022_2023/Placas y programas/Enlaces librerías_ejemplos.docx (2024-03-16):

Enlaces CanSat 2022/2023


LilyGo T-Beam:

https://github.com/glacierjay/T_beam ← Librerías + ejemplos (GPS y LoRa).

https://github.com/LilyGO/TTGO-T-Beam ← Más ejemplos.

https://tinymicros.com/wiki/TTGO_T-Beam ← Especificaciones técnicas.

Librerías:

https://github.com/sandeepmistry/arduino-LoRa ← Librería LoRa.

http://arduiniana.org/libraries/tinygpsplus/ ← TinyGPS++


Problema GPS:

https://meshtastic.discourse.group/t/t-beam-gps-problems-hardware/481/8 ← Tiene el mismo problema que nosotros.

https://stackoverflow.com/questions/68083295/why-i-cant-get-gps-data-from-ttgo-tbeam-t22-v1-1-is-there-any-problem-with-my ← Otro con el mismo problema (Enlace documento README)

https://www.aeq-web.com/ttgo-lilygo-esp32-board-gps-signal-problem-ublox-neo-6/?lang=en ← Solución te quiero

ESP32:


PINOUT de la ESP32 (https://randomnerdtutorials.com/esp32-pinout-reference-gpios/)

Usando el LoRa con el ESP32 (https://randomnerdtutorials.com/esp32-lora-rfm95-transceiver-arduino-ide/)


Nota: Usa los pines del VSPI por defecto.

ESP 32 T-BEAM

https://www.instructables.com/MPU6050-Setup-and-Calibration-Guide/

gnd → GND

miso → 19

mosi →23 dio0 → 25

sck → 18 VCC → 5V

nss → 5

rst → 26

Diferencias de char array vs String() (https://forum.arduino.cc/t/difference-between-char-array-and-string/603608/5)

Limpiar array (Valores null) (https://arduino.stackexchange.com/questions/3167/clear-existing-array-when-getting-new-serial-command)

https://javl.github.io/image2cpp/

sd problem (https://www.reddit.com/r/esp32/comments/j7jiyh/stuck_on_spi_with_the_ttgo_tbeam/)

solucion (?) serial (https://forum.arduino.cc/t/arduino-esp32-import-error-no-module-named-serial/932371/5)

solucion architecture (https://github.com/arduino/arduino-cli/issues/1590)

Problemas servo:

https://forum.arduino.cc/t/servo-gone-crazy-moves-without-me-sending-command/74814/6

https://forum.arduino.cc/t/servo-moving-on-its-own/1015174

- Probar librería servo en la arduino 1, el ejemplo “Sweep”, para comprobar y rastrear el error

UI bonita (https://www.instructables.com/Design-a-Fancy-GUI-for-Your-Project/)

Avion processing (https://www.reddit.com/r/arduino/comments/zreoc9/not_an_original_project_but_still_funny_to/)

https://create.arduino.cc/projecthub/najad/interfacing-and-displaying-images-on-oled-59344a

https://diyusthad.com/image2cpp

Solución SD (https://github.com/Xinyuan-LilyGO/LilyGo-LoRa-Series/issues/41)

https://www.circuitgeeks.com/oled-display-arduino/

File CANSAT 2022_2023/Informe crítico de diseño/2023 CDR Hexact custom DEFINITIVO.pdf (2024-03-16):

# HEXACT -CDR

## (Critical Design Review)


Hexact 2022 - 2023

# Índice:

Índice: | 1
Introducción | 2
El equipo: | 2
Objetivos de la misión. | 2
Vídeo presentación. | 2
Misión primaria y secundaria. | 3
Misión primaria. | 3
Medida de presión y temperatura. | 3
Diseño del paracaídas. | 4
Análisis de datos | 5
Diseño del CanSat | 6
Diseño 3D | 6
Diseño electrónico | 7
Misión secundaria | 8
Dispersor de semillas. | 8
Localización del dispositivo. | 8
Planificación | 9
Presupuesto | 10
Plan de difusión y patrocinio | 11

# Introducción

El desafío CanSat es una iniciativa de la Agencia Espacial Europea que desafía a estudiantes de toda Europa a construir y lanzar un mini satélite del tamaño de una lata de refresco. Cuando se nos habló de la existencia de este proyecto, nuestro equipo no dudó en ponerse manos a la obra. Nos motiva nuestra ambición, dedicación y capacidad a la hora de resolver problemas, además de nuestro deseo de superación y de mejora, puesto que ya participamos el año anterior y estamos seguros de que podemos hacerlo aún mejor. Nos hace especial ilusión participar de nuevo este año para así demostrar de lo que somos capaces y mostrar lo que con mucho esfuerzo hemos creado.

## El equipo:

- Alejandro Chacón Pérez → Códigos del satélite y las estaciones tierra, diseño de la electrónica.
- David González Diosdado → Código de processing, análisis de datos y ayuda en diseño en 3D.
- Antonio Jesús Suarez Gómez → Diseño en 3D, soldadura y montaje de las antenas.
- Adrián Durán Perdigones → Edición de los videos introductorios y diseño del logo.
- Miriam Ganaza Gómez → Diseño y fabricación del paracaídas.
- Iker Espinosa Algeciras → Ayuda con las redes sociales.
- Profesor responsable: Aurelio Gallardo (aurelio@seritium.es).

Instituto IES Seritium (11700767) - Jerez de la Frontera

Objetivos de la misión.

Nuestros objetivos son:

1. Análisis con precisión de las condiciones medioambientales (Presión y temperatura) de la zona de lanzamiento.
2. Dispersión de semillas controlada durante el vuelo.
3. Análisis del estado del satélite durante el vuelo y recuperación para su reutilización una vez finalizada la misión.
4. Crear una base de datos didáctica para ayudar e incentivar a futuras generaciones de estudiantes que decidan participar en el proyecto CanSat.
5. Divertirnos y aprender.

Vídeo presentación.

Vídeo presentación de nuestro proyecto CanSat. (https://youtu.be/FIYeHxksmDY)

Misión primaria y secundaria.

El esquema de vuelo del proyecto se divide en 2 partes:

1. Recogida y procesamiento de datos, así como expulsión periódica de semillas, que toma lugar en el CanSat
2. Recibo y procesamiento de dichos datos, que incluye: Desempaquetado, almacenamiento en la tarjeta SD, mostrado por pantalla y post-procesamiento en Processing para obtener la posición y tablas de los datos.

Los datos que recogeremos serán almacenados en la tarjeta SD, e incluyen: Temperatura, presión barométrica (y derivada, la altura), aceleración, ángulo de inclinación y distancia satélite-base.

Utilizamos, como placa procesadora, una ESP32 v4, que nos da una gran capacidad de procesamiento y un alto número de pines útiles. Elaboramos, asimismo, una PCB personalizada, que nos permite montar todos los sensores y componentes de manera segura y eficiente.

Para la estación de tierra, decidimos usar la placa de desarrollo LILYGO T-BEAM ESP32, que, además de proporcionarnos multitud de pines con los que trabajar, dispone, de manera integrada, de módulo de radio Lora y de chip GPS, muy útiles para el funcionamiento de muestras misiones primarias y secundarias.

Todo el proyecto, tanto el dispositivo CanSat como las estaciones de tierra, han sido programados en Arduino, usando la IDE 2.0.3 oficial.

Misión primaria.

Medida de presión y temperatura.

Como misión primaria, encontramos la medida de presión y temperatura. Conseguiremos estos datos con el sensor GY-87, ubicado en el interior de la carcasa del CanSat. A través del módulo LoRa de telecomunicaciones, enviamos los datos a las estaciones de tierra en forma de un sólo paquete con toda la información (Tanto de la misión primaria como secundaria) concatenada.


Elegimos este sensor porque, aparte de las medidas de temperatura y presión, nos proporciona también datos de aceleración y giroscopio, muy útiles para conocer el estado del satélite en su descenso, todo condensado en un sólo sensor.

Los programas siguen los siguientes esquemas. Diferenciamos entre el programa del satélite y el programa de las estaciones de tierra.


Diseño del paracaídas.

Teniendo como referencia nuestro proyecto CanSat de anteriores ediciones, decidimos rediseñar nuestro prototipo de paracaídas para que cayera de forma más rápida y precisa, aun conservando una velocidad regulada para evitar un impacto fatal.

El paracaídas está fabricado con tela especializada de paracaídas, con cuerda de tanza reforzada para unirla al
CanSat. Sacamos la superficie necesaria para nuestro
paracaídas igualando la fuerza gravitatoria con la de


arrastre, teniendo en cuenta el peso deseado y la velocidad a la que queríamos que descendiese, para que nuestro aterrizaje sea rápido pero eficaz. Además, decidimos cambiar la forma anterior del paracaídas y hacerlo un hexágono, ya que así conseguimos reducir el uso de materiales aun sujetando la misma cantidad de peso.

Anclajes: las cuerdas del paracaídas se anclan al módulo CANSAT a través de unos orificios en la parte superior.


### Análisis de datos


Los datos recogidos, una vez empaquetados y almacenados en la tarjeta SD de cada base, serán exportados al programa Processing; ésto se hará con bucles metiendo los datos en cadenas tipo float, que se encargará de mostrar, en distintas tablas 2D y 3D, los distintos datos, la posición mediante coordenadas,y los distintos ángulos con un modelo 3d que se gira dependiendo de los datos recibidos. La presión (altura barométrica) y temperatura en una gráfica separada. Asimismo, y usando la distancia a cada estación, calcularemos la posición relativa del dispositivo, que se mostrará con los otros datos y será usada para la rápida y eficiente recuperación del CanSat.

Estas son dos ejemplos de gráficas hechas con Processing y algunos datos de prueba:


## Diseño del CanSat

### Diseño 3D

Peso aproximado: 312g , a falta de algunas modificaciones.

La carcasa de nuestro prototipo ha sido diseñada para dar cabida a los sensores, la placa ESP32, una batería 18650 y al mecanismo de eyección de semillas. La placa y los sensores están colocados en la parte superior, montados en la PCB personalizada en forma de “sandwich” (pieza colocada en el modelo color beige), para aprovechar al máximo el espacio útil. La PCB ha sido diseñada con esta configuración en mente, para posicionar los sensores y los pines de alimentación de la manera más eficiente posible.

En el centro de la PCB encontraremos el sistema de telecomunicaciones (LoRa). En la parte inferior encontramos el servo
(Transparente naranja), el cual mueve el brazo (rosa) que deja caer
las semillas, depositadas desde el tanque (azul)


En la otra mitad encontraremos un modelo de donde va insertada la batería (18650), su respectivo

módulo de carga ,y de forma perpendicular a la base, la antena que irá conectada al Lora. Estos componentes se encuentran en la mitad inferior para proporcionar más estabilidad durante el descenso, colocando la mayor cantidad de masa lo más bajo posible para alterar el centro de gravedad.

En los laterales exteriores, diseñamos unas hendiduras donde colocar bisagras metálicas, que proporcionan mayor resistencia al prototipo, aun manteniendo la funcionalidad de cofre.

El dispositivo está diseñado para que sea fácil de manipular: dispondrá de salidas USB al exterior que permiten tanto recargar las baterías interiores como acceder a la placa directamente para su reprogramación o ajustes vía comunicación serie del propio programa. Lo ideamos todo para que pueda servir como base para futuras generaciones de participantes de CanSat y como elemento didáctico a la hora de enseñar programación, diseño y electrónica.


La antena también ha sido diseñada e impresa en 3D, con especial cuidado en mantener las medidas correctas para antenas Yagi pero con un diseño práctico: está formada por partes desmontables para facilitar su almacenaje, y dispone de 2 mangos para poder sujetarla cómodamente .


### Diseño electrónico

Respecto al diseño electrónico, las estaciones de tierra son los módulos LILYGO T-BEAM ESP32 a las que hemos adaptado dos módulos distintos: grabador microSD y pantalla OLED.

El módulo CanSat sí tiene un esquema propio basado en un módulo ESP32, principalmente debido a la búsqueda de reducir el tamaño y la administración de la energía. Este incluye el diseño de una placa PCB y técnicas de soldadura SMD para el módulo LoRa 868Mhz, así como conexiones para el módulo multisensor GY-87 y el servo necesario para la misión secundaria del lanzamiento de semillas.

Ideamos el diseño electrónico en el CanSat con la intención de obtener un sistema que, con un sólo interruptor, pudiera cambiar entre estado de subida de código, apagado y encendido a través de las baterías, ya que ambas fuentes de alimentación (Batería y USB) no podían solaparse. Por ello, diseñamos el circuito y la PCB siguiendo la siguiente tabla:

| Encendido | Datos | Apagado
Batería | 1 | 0 | 0
USB | 0 | 1 | 0

De donde extraemos lo siguiente:
1. Si el interruptor está en posición de la batería, sólo está alimentará a la placa.
2. Si el interruptor está en posición de USB y el USB está conectado, la placa funcionará debido a la corriente suministrada por éste. (A excepción del servo, debido a la falta de intensidad en el circuito).
3. Si el interruptor está en posición de USB y el USB está desconectado, el CanSat estará apagado, ya que nada lo alimenta.

Así conseguimos un circuito que combina las baterías y la accesibilidad al puerto USB para re-programaciones y ajustes vía puerto serie sin necesidad de preocuparnos por conflictos batería-USB.

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

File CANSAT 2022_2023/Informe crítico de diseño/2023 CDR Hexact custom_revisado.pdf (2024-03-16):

# HEXACT -CDR

## (Critical Design Review)


Hexact 2022 - 2023

# Índice:

Índice: | 1
Introducción: | 2
El equipo: | 2
Objetivos de la misión. | 2
Vídeo presentación. | 2
Misión primaria y secundaria. | 3
Misión primaria. | 3
Medida de presión y temperatura. | 3
Diseño del paracaídas. | 4
Análisis de datos | 5
Diseño del CanSat | 5
Misión secundaria | 7
Dispersor de semillas. | 7
Localización del dispositivo. | 7
Planificación | 8
Presupuesto | 8
Plan de difusión y patrocinio | 10
Notas | 10

# Introducción:

## El equipo:
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

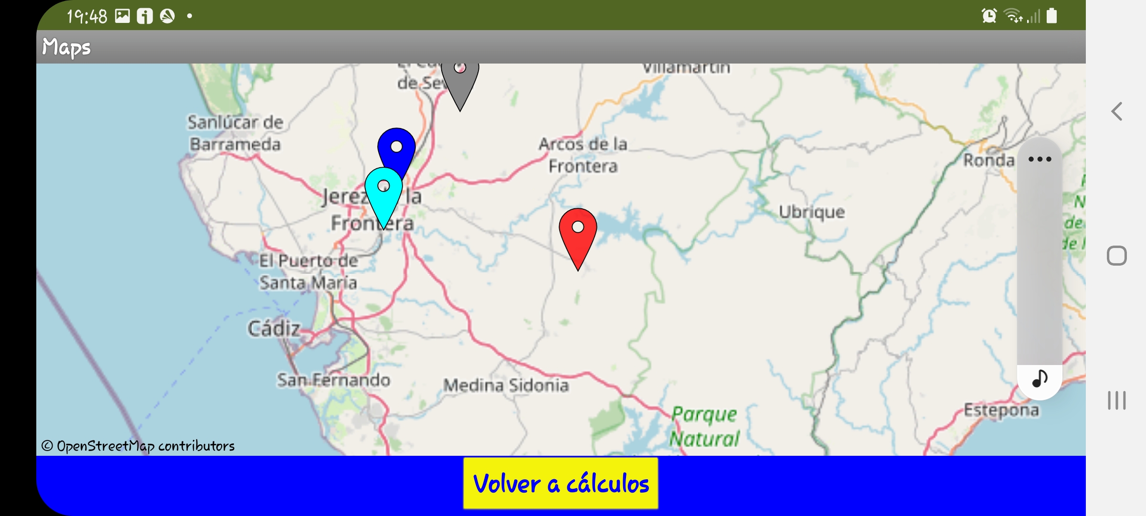
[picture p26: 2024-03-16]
CANSAT 2022_2023/MATEMATICAS/Screenshot_20230426-194832.jpg

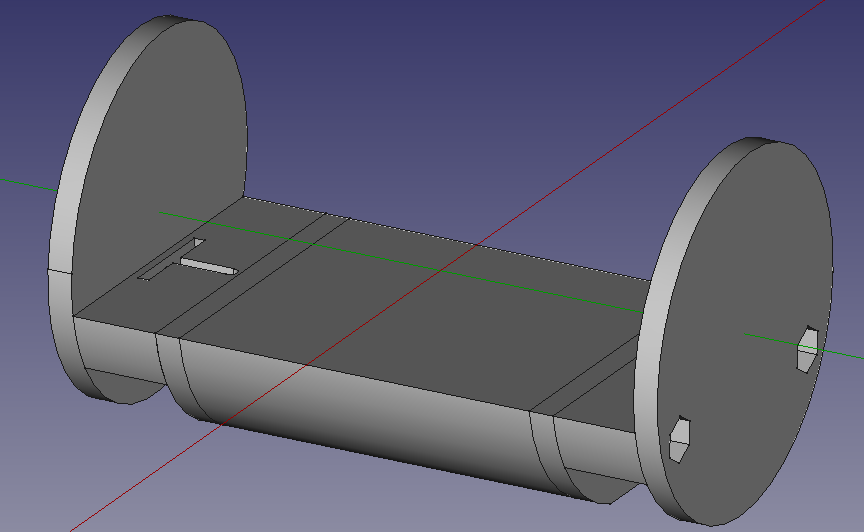
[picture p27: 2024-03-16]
CANSAT 2021_2022/Solucion1.png

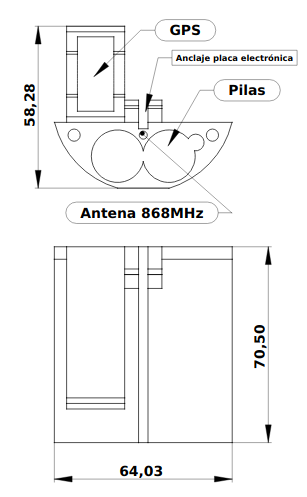
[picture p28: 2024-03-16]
CANSAT 2021_2022/Plano_habitaculo_Pila.png

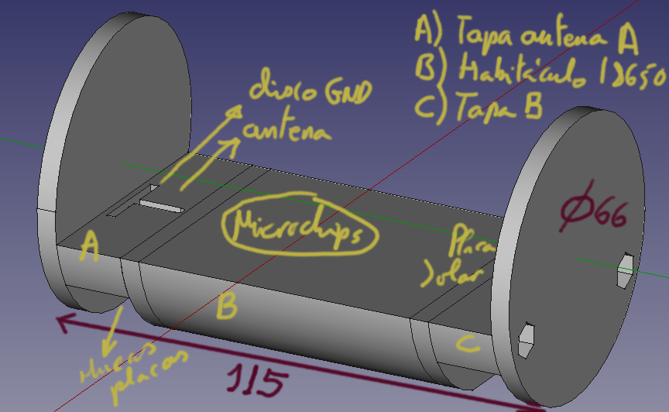
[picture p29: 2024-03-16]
CANSAT 2021_2022/Solucion1_Medidas.png

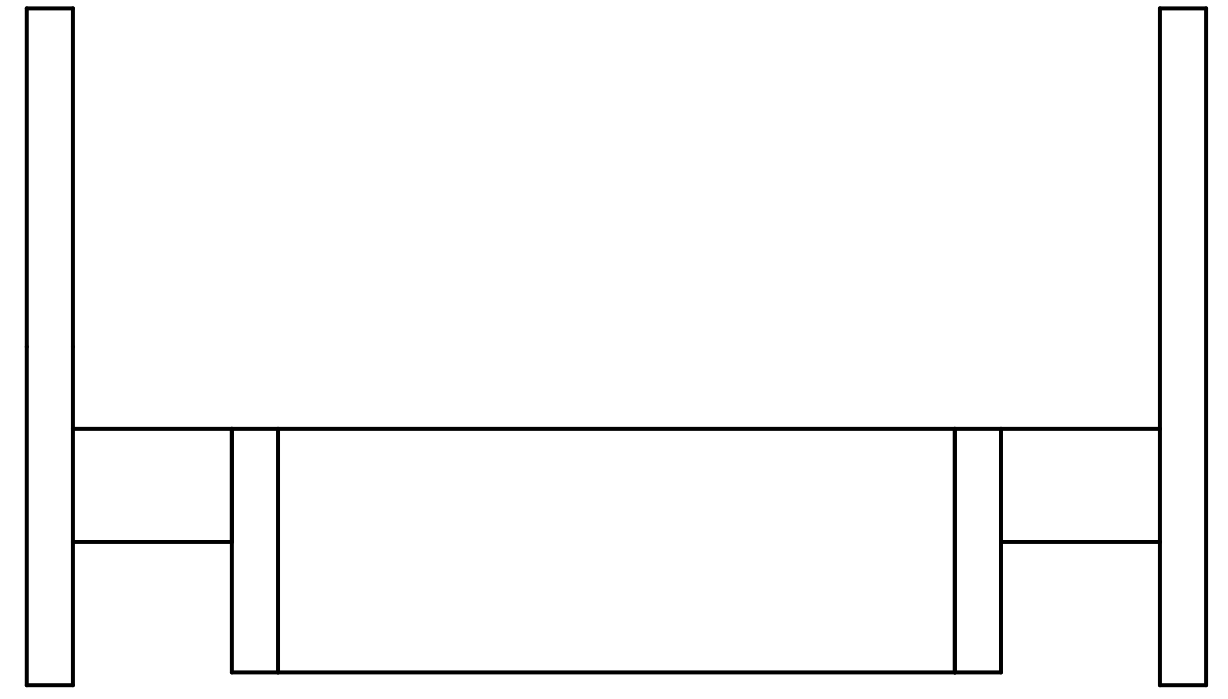
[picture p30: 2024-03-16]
CANSAT 2021_2022/Paracaidas.png

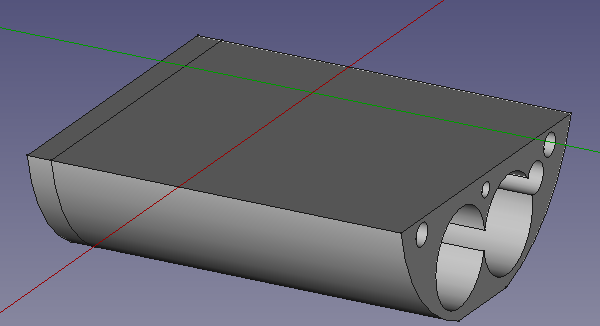
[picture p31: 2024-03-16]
CANSAT 2021_2022/Solucion2.png

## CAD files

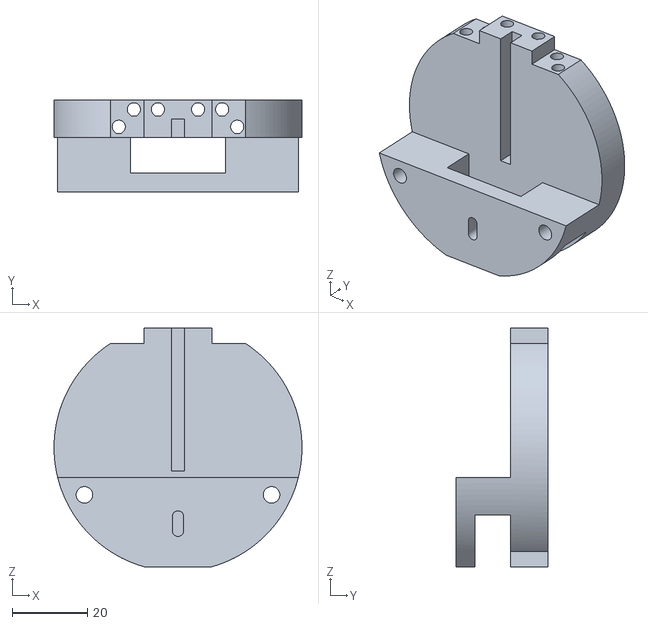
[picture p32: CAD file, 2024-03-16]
CANSAT 2021_2022/Anteriores_3D/Corte_piezas_DEF_2-Lateral_B.stl
66.0 x 24.5 x 63.5

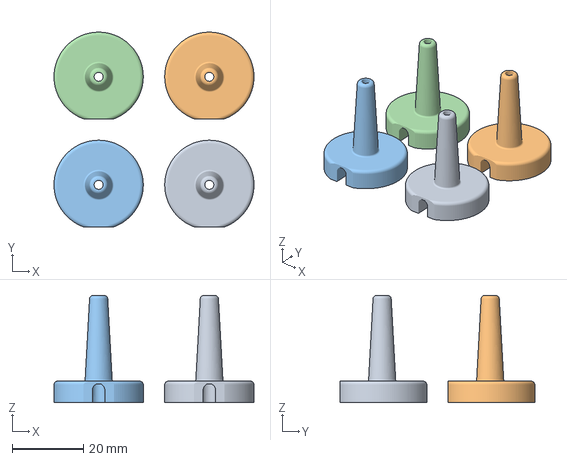
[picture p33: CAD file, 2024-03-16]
CANSAT 2021_2022/Base_antena_impresion_3D/Base_antena_mejorada_6#1.3mf
56.0 x 54.5 x 30.0 mm

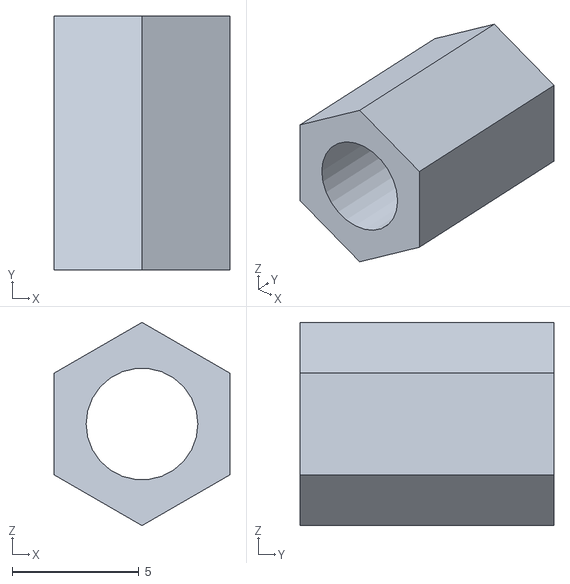
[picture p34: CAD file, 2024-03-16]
CANSAT 2021_2022/Impresion_DEF2/Pasante2.stl
6.93 x 10.0 x 8.00

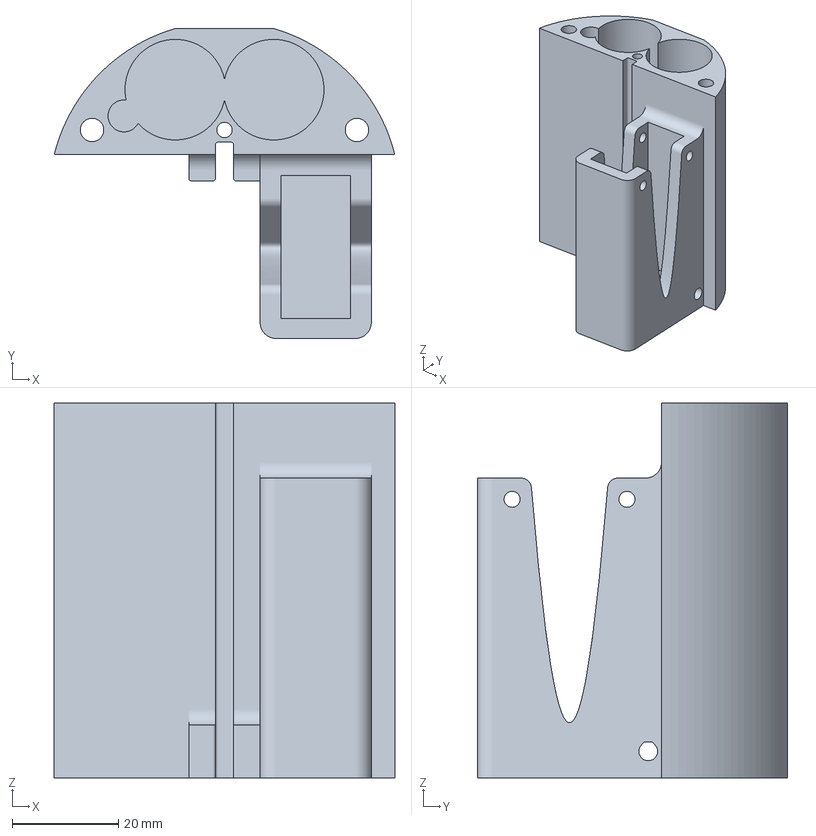
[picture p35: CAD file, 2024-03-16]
CANSAT 2021_2022/Impresion_DEF3/CE3PRO_DEF_3_Habitaculo_Pila.3mf
64.0 x 58.3 x 70.5 mm

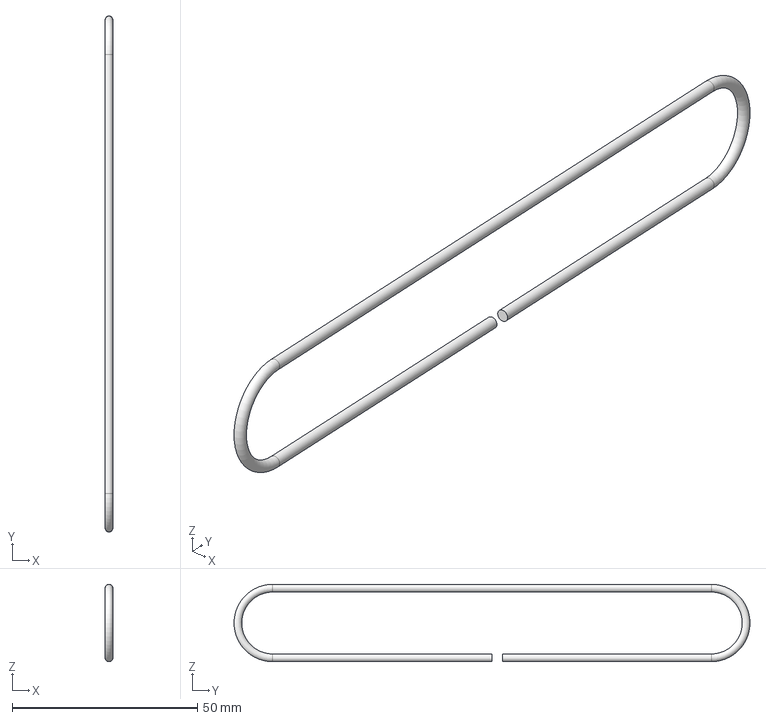
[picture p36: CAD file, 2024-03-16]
CANSAT 2021_2022/YAGI/yagi.FCStd
2.10 x 139.3 x 20.9 mm

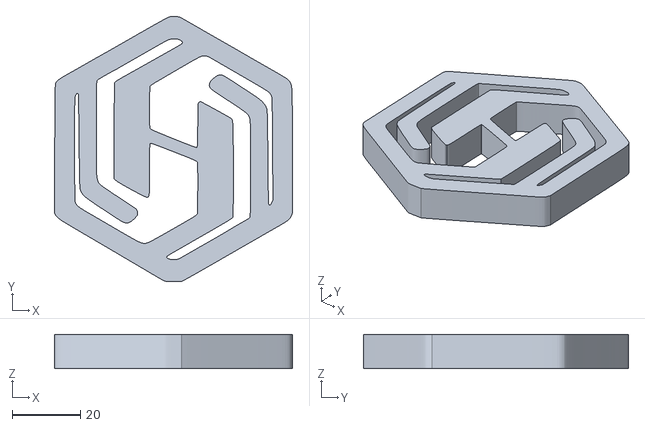
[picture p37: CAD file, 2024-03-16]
CANSAT 2022_2023/Carpeta que para nada acabo de crear con el logo y el stl del cansat/Loguito CanSat.stl
70.0 x 78.0 x 10.0

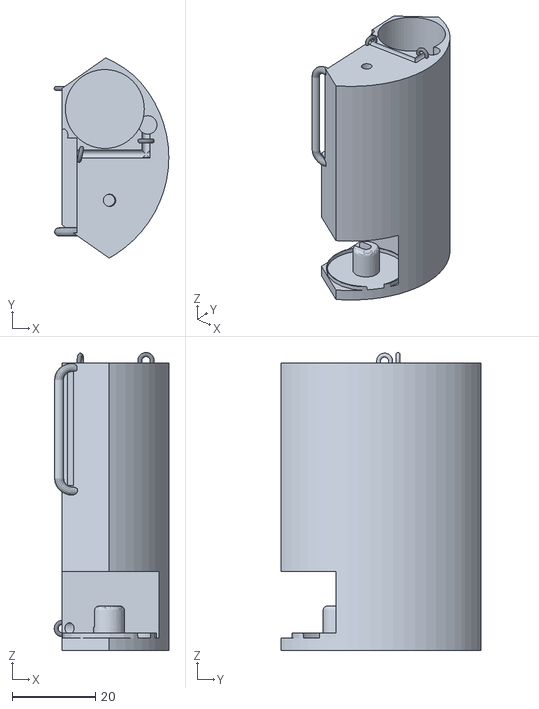
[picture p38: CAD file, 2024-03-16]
CANSAT 2022_2023/Modelos 3D/Modelos en OBJ y STL/CompartimentoBateria.stl
27.6 x 48.2 x 71.8

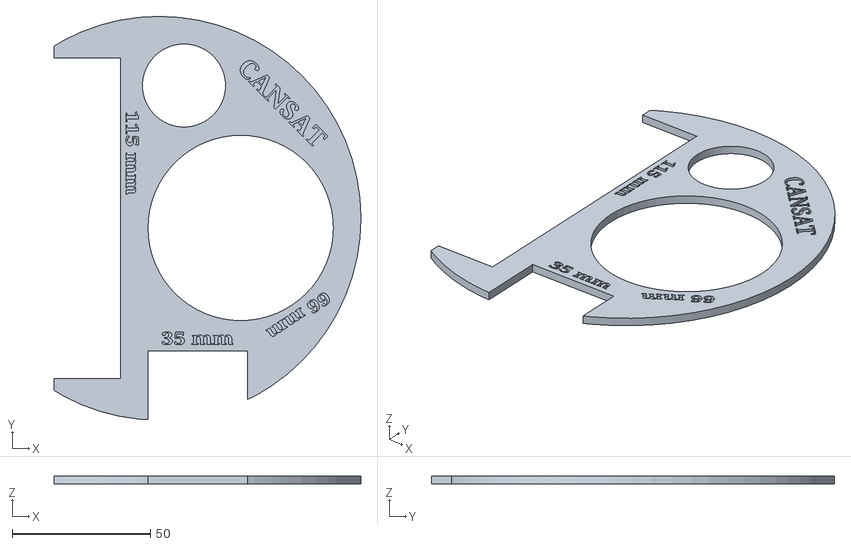
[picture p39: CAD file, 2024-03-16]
CANSAT 2022_2023/VERIFICACION/InstrumentoVerificacion.stl
111.0 x 145.8 x 3.00

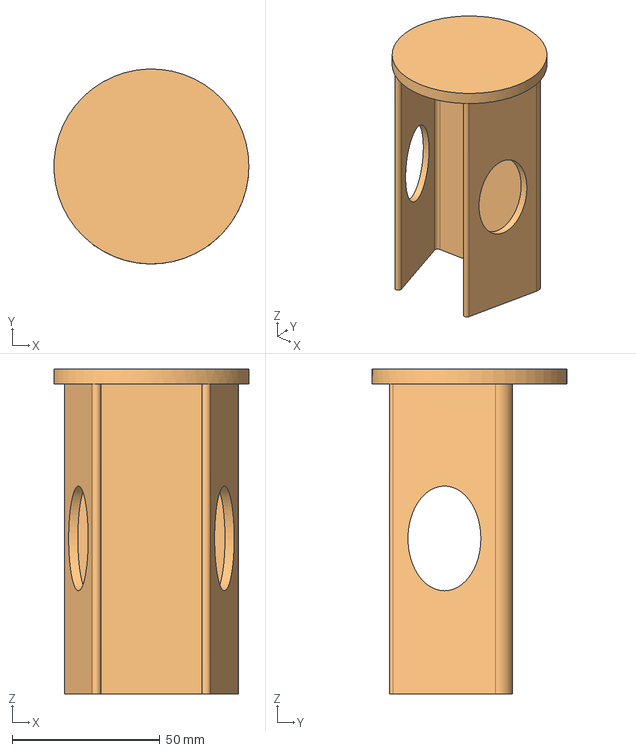
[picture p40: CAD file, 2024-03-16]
CANSAT 2021_2022/Anteriores_3D/Corte_piezas.FCStd
65.9 x 66.0 x 110.0 mm
Relleno
Pieza principal

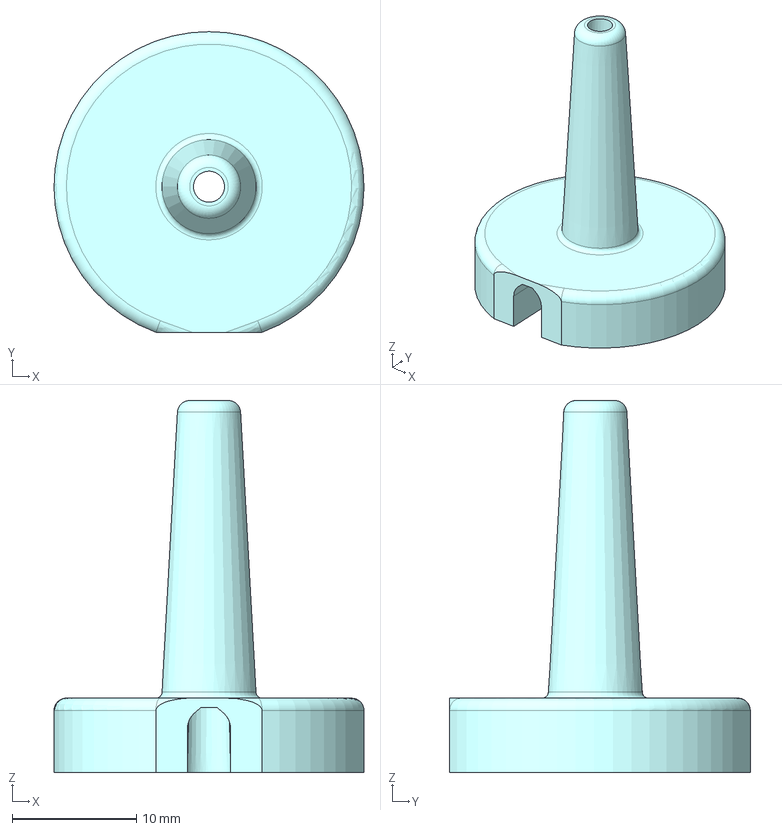
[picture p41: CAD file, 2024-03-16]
CANSAT 2021_2022/Base_antena_impresion_3D/Base_antena.FCStd
25.0 x 24.2 x 30.0 mm

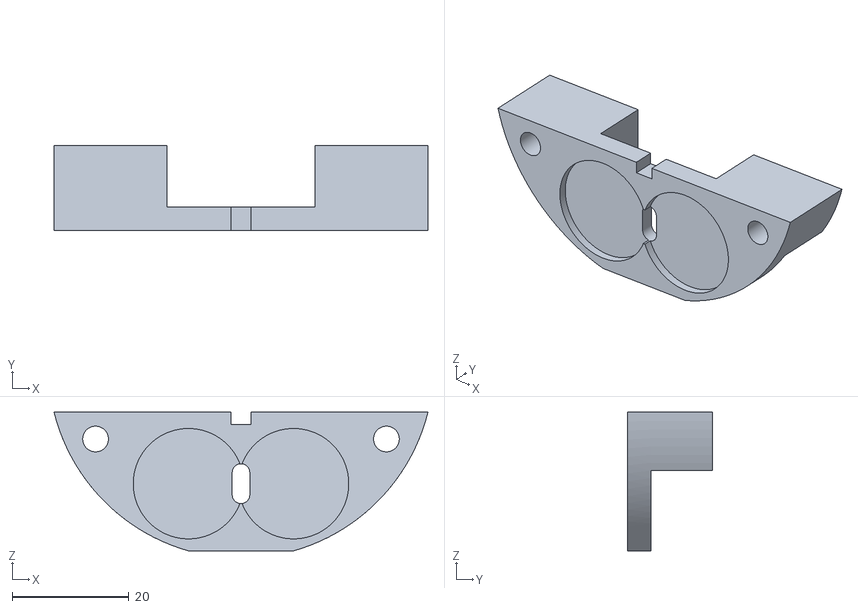
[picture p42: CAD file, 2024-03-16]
CANSAT 2021_2022/Impresion_DEF2/Tapa_Pilas.stl
64.0 x 14.5 x 23.7

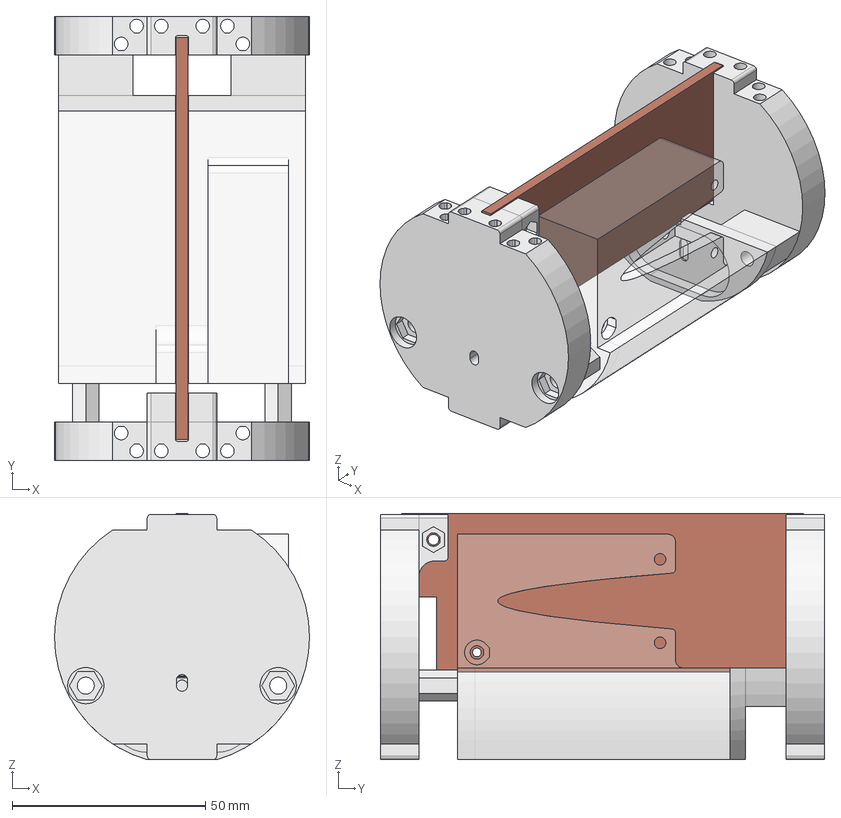
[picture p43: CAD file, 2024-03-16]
CANSAT 2021_2022/Impresion_DEF4/Corte_piezas_DEF_4.FCStd
66.0 x 115.0 x 63.7 mm
Habitaculo_Pila
Placa_electronica
Pasante1
Pasante2
LateralA
Tapa_Pilas
LateralB

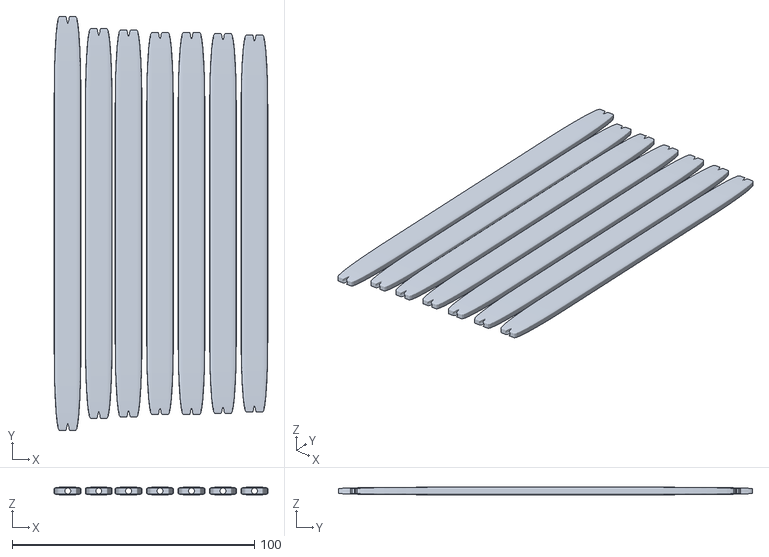
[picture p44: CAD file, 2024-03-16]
CANSAT 2022_2023/Modelos 3D/Modelos en OBJ y STL/Vainas.stl
88.2 x 171.0 x 3.10

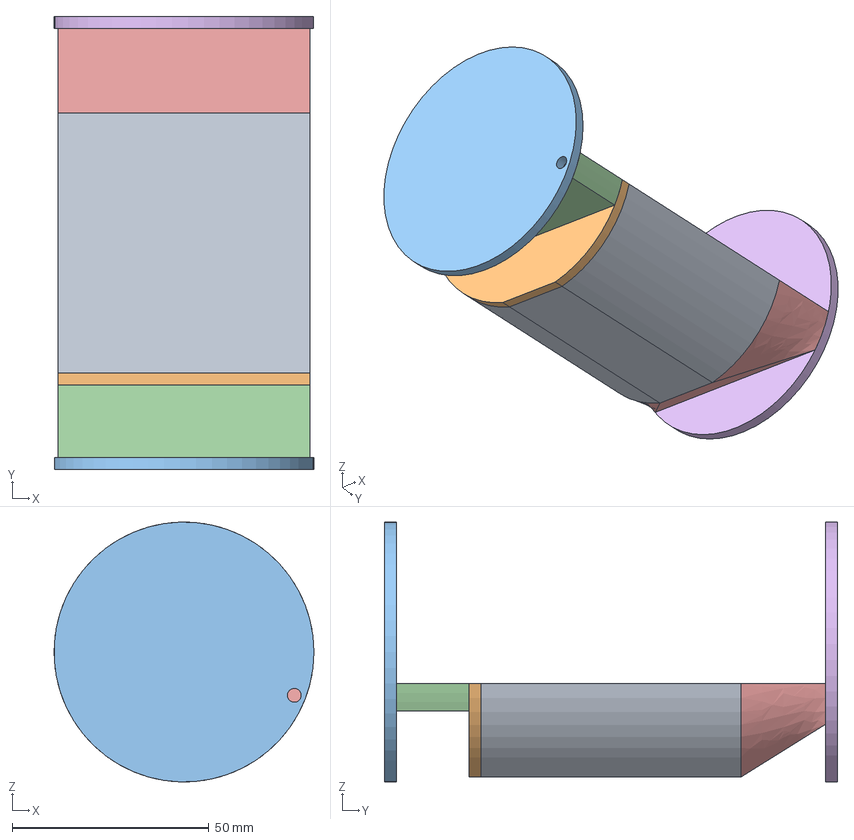
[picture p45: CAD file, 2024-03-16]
CANSAT 2021_2022/Anteriores_3D/Corte_piezas3.FCStd
66.0 x 115.0 x 66.0 mm
Habitaculo_Pilas
TapaPilas
TapaLateralA
Pieza_LateralA
TapaLateralB

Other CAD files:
CANSAT 2021_2022/Impresion_DEF4/Corte_piezas_DEF_4-Pasante1.stl
CANSAT 2021_2022/Impresion_DEF3/DEF_3_Habitaculo_Pila.stl
CANSAT 2021_2022/Anteriores_3D/Corte_piezas2.FCStd
CANSAT 2021_2022/Anteriores_3D/Corte_piezas4-LateralA.stl
CANSAT 2021_2022/Anteriores_3D/Corte_piezas4.FCStd
CANSAT 2021_2022/Anteriores_3D/Corte_piezas_DEF_1.FCStd
CANSAT 2021_2022/Anteriores_3D/Corte_piezas_DEF_2-LateralA.stl
CANSAT 2021_2022/Anteriores_3D/Corte_piezas_DEF_3.FCStd
CANSAT 2021_2022/Base_antena_impresion_3D/Base_Antena_mejorada.stl
CANSAT 2021_2022/Base_antena_impresion_3D/Base_antena.3mf
CANSAT 2021_2022/Base_antena_impresion_3D/Base_antena.stl
CANSAT 2021_2022/Impresion_DEF2/Corte_piezas_DEF_2.FCStd
CANSAT 2021_2022/Impresion_DEF2/Habitaculo_Pila.stl
CANSAT 2021_2022/Impresion_DEF2/Habitaculo_mas_Tapa_habitaculo.3mf
CANSAT 2021_2022/Impresion_DEF2/LateralA.stl
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

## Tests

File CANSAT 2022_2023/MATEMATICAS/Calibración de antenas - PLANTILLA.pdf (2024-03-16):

### Calibración de antenas

Punto fijo: | altura punto fijo (m) | Punto fijo LAT y LON | Radio Tierra (km)
Punto móvil: | | | | 6371
Nº | Latitud | Longitud | altura (m) | RSSI | distancia ort. (m) | distancia lineal (m)
1 | | | | | 0 | 0
2 | | | | | 0 | 0
3 | | | | | 0 | 0
4 | | | | | 0 | 0
5 | | | | | 0 | 0
6 | | | | | 0 | 0
7 | | | | | 0 | 0
8 | | | | | 0 | 0
9 | | | | | 0 | 0
10 | | | | | 0 | 0
11 | | | | | 0 | 0
12 | | | | | 0 | 0
13 | | | | | 0 | 0
14 | | | | | 0 | 0
15 | | | | | 0 | 0
16 | | | | | 0 | 0
17 | | | | | 0 | 0
18 | | | | | 0 | 0
19 | | | | | 0 | 0
20 | | | | | 0 | 0
21 | | | | | 0 | 0
22 | | | | | 0 | 0
23 | | | | | 0 | 0
24 | | | | | 0 | 0
25 | | | | | 0 | 0
26 | | | | | 0 | 0
27 | | | | | 0 | 0
28 | | | | | 0 | 0
29 | | | | | 0 | 0
30 | | | | | 0 | 0
31 | | | | | 0 | 0
32 | | | | | 0 | 0
33 | | | | | 0 | 0
34 | | | | | 0 | 0
35 | | | | | 0 | 0
36 | | | | | 0 | 0
37 | | | | | 0 | 0
38 | | | | | 0 | 0
39 | | | | | 0 | 0
40 | | | | | 0 | 0
41 | | | | | 0 | 0
42 | | | | | 0 | 0
43 | | | | | 0 | 0
44 | | | | | 0 | 0
45 | | | | | 0 | 0
46 | | | | | 0 | 0
47 | | | | | 0 | 0
48 | | | | | 0 | 0
49 | | | | | 0 | 0
50 | | | | | 0 | 0

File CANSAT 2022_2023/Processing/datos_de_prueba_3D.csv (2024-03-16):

X | Y | Z
0 | 18,6 | 82,77
1 | 0,83 | 74,92
2 | 29,42 | 58,26
3 | 45,97 | 11,04
4 | 4,73 | 66,09
5 | 74,34 | 6,52
6 | 71,54 | 31,73
7 | 45,56 | 92,12
8 | 99,2 | 37,73
9 | 31,06 | 4,99
10 | 100,91 | 27,98
11 | 83,03 | 18,76
12 | 70,15 | 78,1
13 | 25,36 | 24,91
14 | 3,15 | 84,79
15 | 85,55 | 20,88
16 | 27,49 | 29,92
17 | 32,81 | 87,87
18 | 44,33 | 29,84
19 | 29,38 | 42,11
20 | 36,71 | 46,95

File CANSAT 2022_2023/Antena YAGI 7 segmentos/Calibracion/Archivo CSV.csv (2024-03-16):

WP/TRK | TRK ID | Long | Lat | Alt (m) | UTC | CEST
WP |  | -6.15362347 | 36.66589298 | 57 | 2023-04-20T16:52:11Z | 18:52:11
WP |  | -6.15264563 | 36.66509683 | 62 | 2023-04-20T16:53:48Z | 18:53:48
WP |  | -6.15312575 | 36.66418962 | 59 | 2023-04-20T16:56:02Z | 18:56:02
WP |  | -6.15219603 | 36.66337910 | 59 | 2023-04-20T16:57:38Z | 18:57:38
WP |  | -6.15127754 | 36.66259350 | 60 | 2023-04-20T17:00:14Z | 19:00:14
WP |  | -6.14989294 | 36.66237166 | 56 | 2023-04-20T17:04:23Z | 19:04:23
WP |  | -6.14733027 | 36.66317612 | 65 | 2023-04-20T17:08:29Z | 19:08:29
WP |  | -6.14557656 | 36.66368286 | 57 | 2023-04-20T17:11:04Z | 19:11:04
WP |  | -6.14393126 | 36.66391735 | 58 | 2023-04-20T17:13:09Z | 19:13:09
WP |  | -6.14281592 | 36.66233155 | 60 | 2023-04-20T17:15:48Z | 19:15:48
WP |  | -6.14015644 | 36.66069273 | 62 | 2023-04-20T17:19:39Z | 19:19:39
WP |  | -6.13956475 | 36.66365187 | 55 | 2023-04-20T17:22:55Z | 19:22:55
WP |  | -6.14128285 | 36.66592880 | 55 | 2023-04-20T17:25:27.000148Z | 19:25:27
WP |  | -6.14438343 | 36.66466486 | 53 | 2023-04-20T17:29:28Z | 19:29:28
WP |  | -6.14669521 | 36.66406871 | 63 | 2023-04-20T17:31:35Z | 19:31:35
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

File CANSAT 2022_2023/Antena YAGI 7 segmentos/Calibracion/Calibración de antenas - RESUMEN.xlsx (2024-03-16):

D | P1 | P2 | P3
422.3955034 | 90 | 90 | 90
532.1880666 | 115 | 94 | 112
616.8664023 | 113 | 101 | 108
725.921774 | 120 | 101 | 106
835.7348277 | 120 | 99
909.9225637 | 115 | 108 | 108
969.5482159 | 107 | 106 | 106
1045.323791 | 120 | 102 | 111
1148.560339 | 120 | 102 | 111
1630.908943 | 119
1502.168472 | 119
1263.358541 | 119
1070.289026 | 121
941.1780932 | 109 | 100 | 109
840.6269727 | 113 | 102 | 112
676.7330748 | 111 | 100 | 106
521.3224183 | 110 | 98 | 108
288.103736 | 113 | 101 | 108
218.9371975 | 110 | 96 | 99

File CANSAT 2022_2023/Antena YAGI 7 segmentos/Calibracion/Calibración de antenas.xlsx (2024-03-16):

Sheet: PLANTILLA
Punto fijo: |  |  | altura punto fijo (m) | Punto fijo LAT y LON |  | Radio Tierra (km) |  |  |  |  |  |  | Cálculo ortodrómico; después d = R * n
Punto móvil: |  |  |  |  |  | 6371
 |  |  |  |  |  |  |  |  |  |  | Paso a distancia en un plano
 | Web que calcula distancia ortodrómicas |  | https://www.tutiempo.net/calcular-distancias.html
 | Web donde obtener información de las alturas: |  | http://www.ign.es/iberpix/
 |  |  |  | Potencia |  |  | d
Nº | Latitud | Longitud | altura (m) | RSSI | distancia ort. (m) | distancia lineal (m) | Distancia rectificada altura (m) | N (rad) | e1 (rad) | e2 (rad) | cos(n) | n
1 |  |  |  |  | 0 | 0 | 0 | 0 | 1.570796327 | 1.570796327 | 1 | 0
2 |  |  |  |  | 0 | 0 | 0 | 0 | 1.570796327 | 1.570796327 | 1 | 0
3 |  |  |  |  | 0 | 0 | 0 | 0 | 1.570796327 | 1.570796327 | 1 | 0
4 |  |  |  |  | 0 | 0 | 0 | 0 | 1.570796327 | 1.570796327 | 1 | 0
5 |  |  |  |  | 0 | 0 | 0 | 0 | 1.570796327 | 1.570796327 | 1 | 0
6 |  |  |  |  | 0 | 0 | 0 | 0 | 1.570796327 | 1.570796327 | 1 | 0
7 |  |  |  |  | 0 | 0 | 0 | 0 | 1.570796327 | 1.570796327 | 1 | 0
8 |  |  |  |  | 0 | 0 | 0 | 0 | 1.570796327 | 1.570796327 | 1 | 0
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

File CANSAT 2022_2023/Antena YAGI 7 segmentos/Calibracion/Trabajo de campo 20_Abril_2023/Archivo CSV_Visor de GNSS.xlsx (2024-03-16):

WP/TRK | TRK ID | Long | Lat | Alt (m) | UTC | CEST
WP |  | -615362347 | 3666589298 | 57 | 2023-04-20T16:52:11Z | 18:52:11 | 36.66589298 | -6.15362347 | 36.66589298 | -6.15362347
WP |  | -615264563 | 3666509683 | 62 | 2023-04-20T16:53:48Z | 18:53:48 | 36.66509683 | -6.15264563 | 36.66509683 | -6.15264563
WP |  | -615312575 | 3666418962 | 59 | 2023-04-20T16:56:02Z | 18:56:02 | 36.66418962 | -6.15312575 | 36.66418962 | -6.15312575
WP |  | -615219603 | 3666337910 | 59 | 2023-04-20T16:57:38Z | 18:57:38 | 36.6633791 | -6.15219603 | 36.6633791 | -6.15219603
WP |  | -615127754 | 3666259350 | 60 | 2023-04-20T17:00:14Z | 19:00:14 | 36.6625935 | -6.15127754 | 36.6625935 | -6.15127754
WP |  | -614989294 | 3666237166 | 56 | 2023-04-20T17:04:23Z | 19:04:23 | 36.66237166 | -6.14989294 | 36.66237166 | -6.14989294
WP |  | -614733027 | 3666317612 | 65 | 2023-04-20T17:08:29Z | 19:08:29 | 36.66317612 | -6.14733027 | 36.66317612 | -6.14733027
WP |  | -614557656 | 3666368286 | 57 | 2023-04-20T17:11:04Z | 19:11:04 | 36.66368286 | -6.14557656 | 36.66368286 | -6.14557656
WP |  | -614393126 | 3666391735 | 58 | 2023-04-20T17:13:09Z | 19:13:09 | 36.66391735 | -6.14393126 | 36.66391735 | -6.14393126
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

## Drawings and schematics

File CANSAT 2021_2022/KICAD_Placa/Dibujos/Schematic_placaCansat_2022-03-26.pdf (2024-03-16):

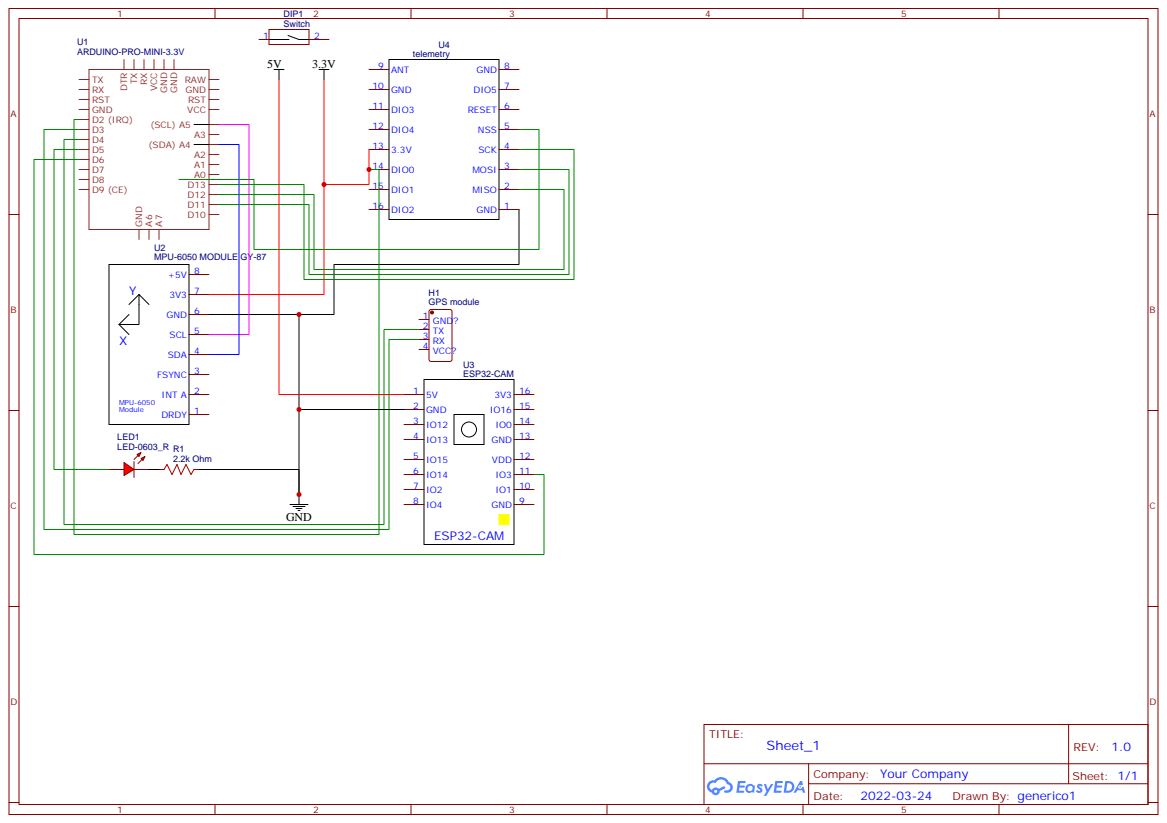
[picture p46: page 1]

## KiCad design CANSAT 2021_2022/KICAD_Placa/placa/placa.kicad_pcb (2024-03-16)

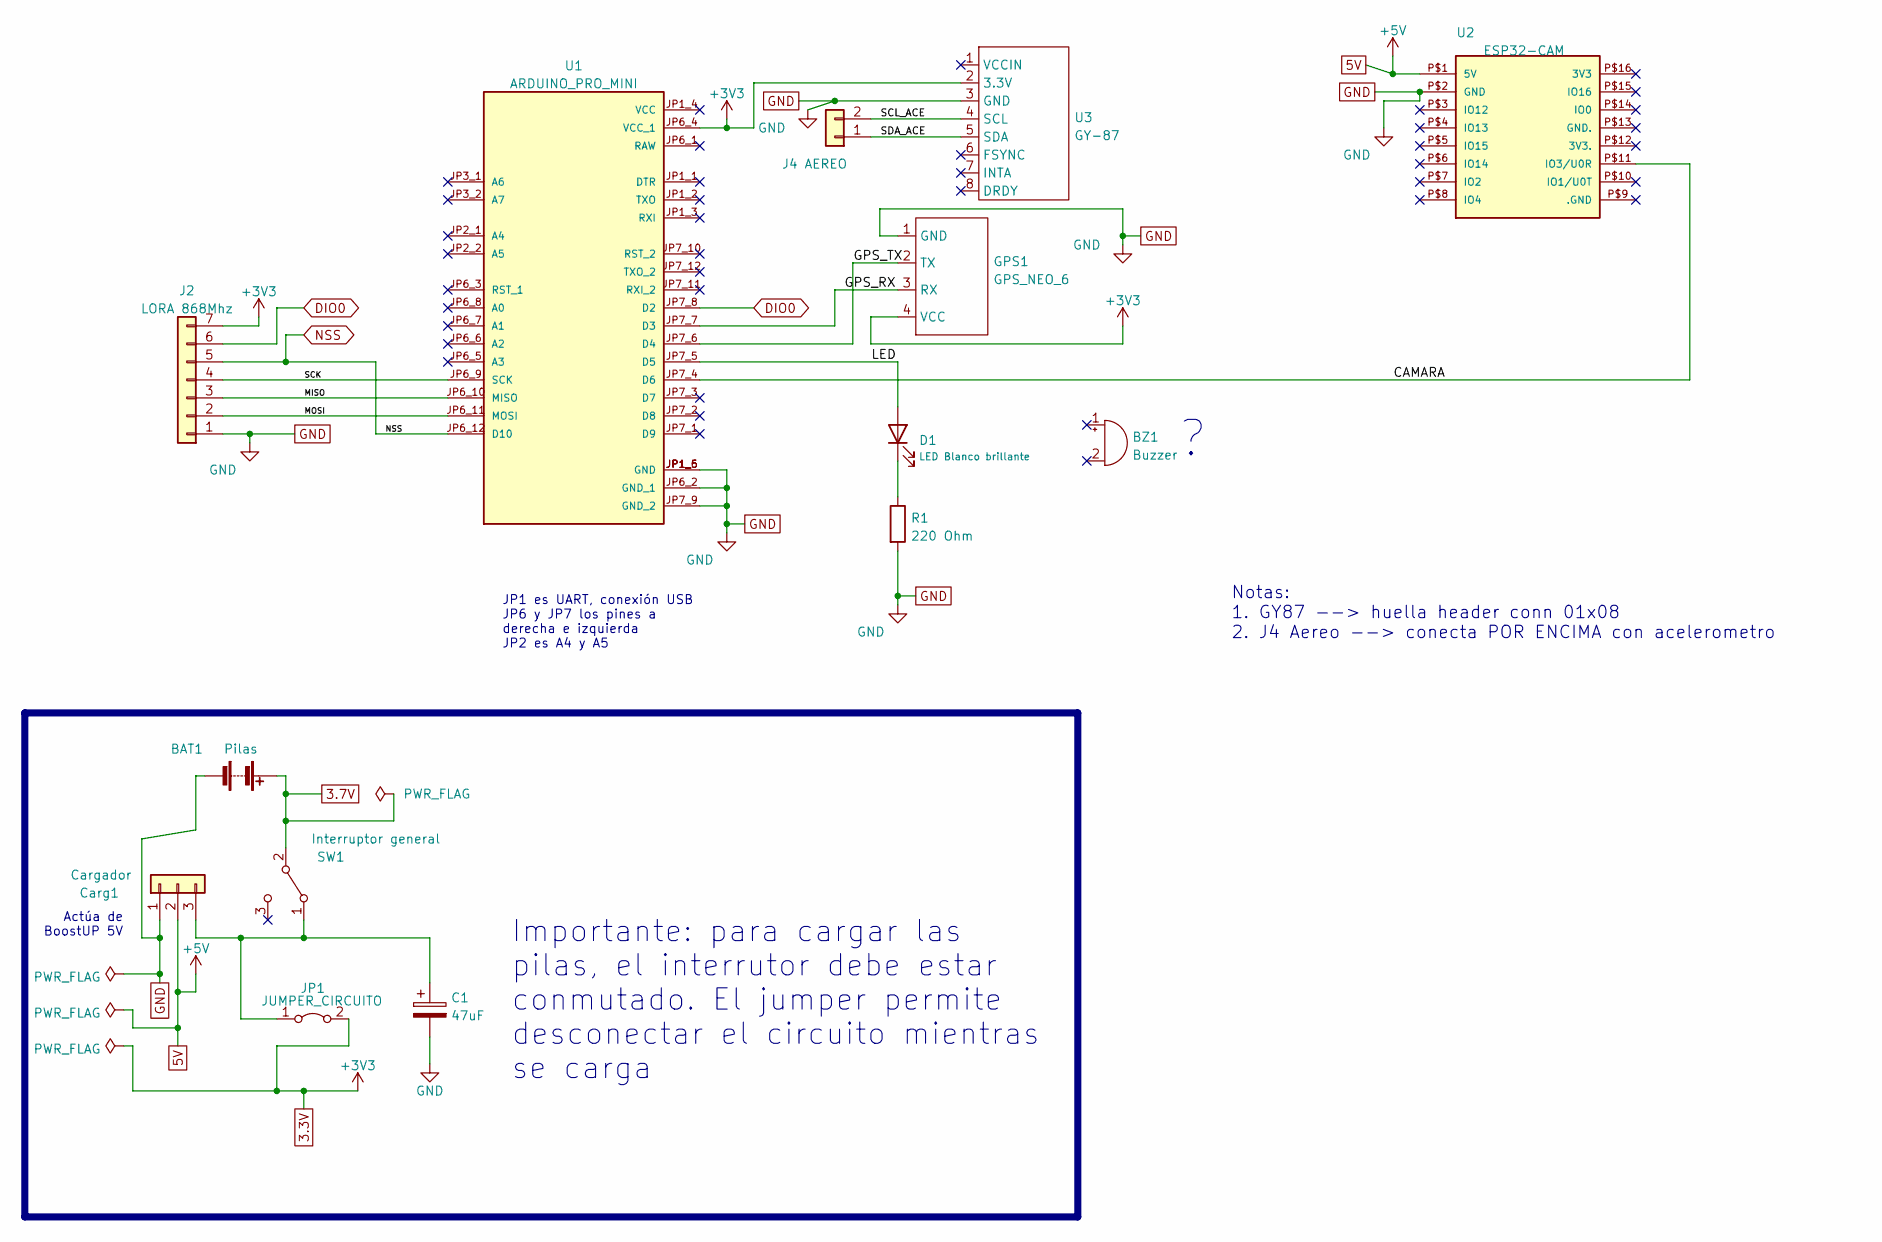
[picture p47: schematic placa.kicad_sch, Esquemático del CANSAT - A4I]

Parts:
BAT1: Pilas; PinHeader_1x02_P2.54mm_Vertical_SMD_Pin1Left
BZ1: Buzzer; Buzzer_15x7.5RM7.6
C1: 47uF; CP_Radial_D8.0mm_P3.50mm
Carg1: Cargador; SolderWire-0.25sqmm_1x03_P4.2mm_D0.65mm_OD1.7mm_Relief
D1: LED Blanco brillante; LED_D5.0mm_Horizontal_O3.81mm_Z3.0mm
GPS1: GPS_NEO_6; PinHeader_1x04_P2.54mm_Vertical
J2: LORA 868Mhz; PinHeader_1x07_P2.54mm_Vertical
J4: AEREO; PinHeader_1x02_P2.54mm_Vertical
JP1: JUMPER_CIRCUITO; PinHeader_1x02_P2.54mm_Vertical
R1: 220 Ohm; R_Axial_DIN0414_L11.9mm_D4.5mm_P5.08mm_Vertical
SW1: Interruptor general; R_Axial_Power_L20.0mm_W6.4mm_P5.08mm_Vertical
U1: ARDUINO_PRO_MINI; MODULE_ARDUINO_PRO_MINI; PARTREV N/A
U2: ESP32-CAM
U3: GY-87; PinHeader_1x08_P2.54mm_Vertical

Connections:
3.3V: GPS1.4 (VCC), J2.7, JP1.2 (B), U1.JP6_4 (VCC_1), U3.2 (3.3V)
3.7V: BAT1.1 (+), SW1.2 (B)
5V: Carg1.2, U2.P$1 (5V)
/MISO: J2.3, U1.JP6_10 (MISO)
/MOSI: J2.2, U1.JP6_11 (MOSI)
/SCK: J2.4, U1.JP6_9 (SCK)
DIO0: J2.6, U1.JP7_8 (D2)
GND: BAT1.2 (-), C1.2, Carg1.1, GPS1.1 (GND), J2.1, R1.2, U1.JP1_5 (GND), U1.JP1_6 (GND), U1.JP6_2 (GND_1), U1.JP7_9 (GND_2), U2.P$2 (GND), U3.3 (GND)
NSS: J2.5, U1.JP6_12 (D10)
unnamed: C1.1, Carg1.3, JP1.1 (A), SW1.1 (A)
unnamed: D1.1 (K), R1.1
unnamed: D1.2 (A), U1.JP7_5 (D5)
unnamed: GPS1.2 (TX), U1.JP7_6 (D4)
unnamed: GPS1.3 (RX), U1.JP7_7 (D3)
unnamed: J4.1, U3.5 (SDA)
unnamed: J4.2, U3.4 (SCL)
unnamed: U1.JP7_4 (D6), U2.P$11 (IO3/U0R)

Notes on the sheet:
JP1 es UART, conexión USB JP6 y JP7 los pines a derecha e izquierda JP2 es A4 y A5
Importante: para cargar las pilas, el interrutor debe estar conmutado. El jumper permite desconectar el circuito mientras se carga
Notas: 1. GY87 --> huella header conn 01x08 2. J4 Aereo --> conecta POR ENCIMA con acelerometro
Actúa de BoostUP 5V

Board: 2 copper layers, 13 parts (0 on the bottom side), 17 nets, no tracks yet.

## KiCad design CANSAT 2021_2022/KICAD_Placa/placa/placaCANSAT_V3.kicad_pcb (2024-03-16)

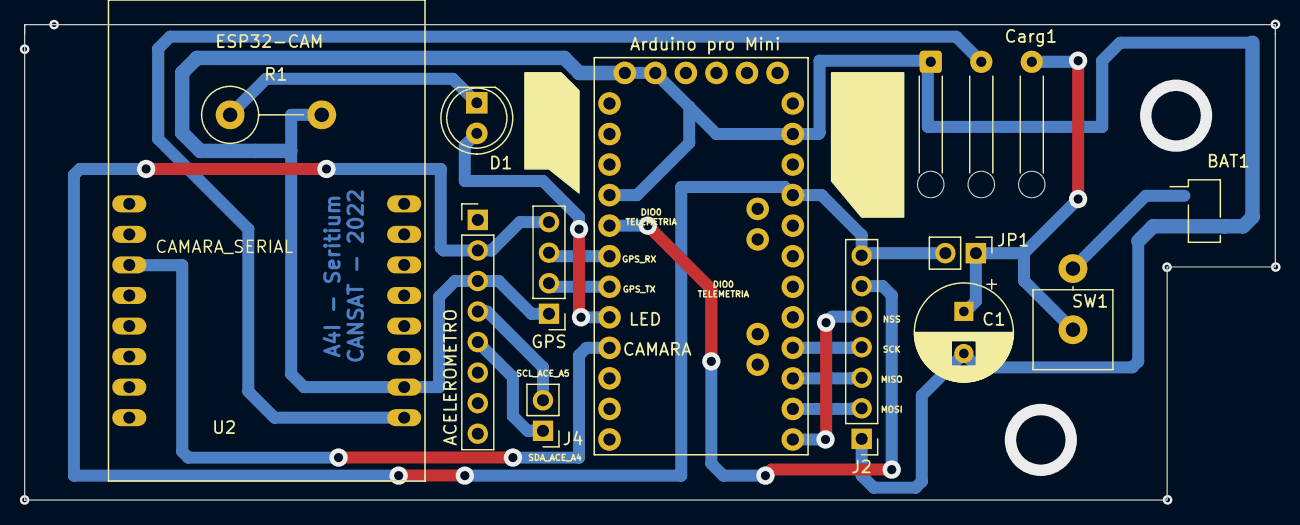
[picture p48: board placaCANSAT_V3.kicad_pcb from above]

Board: 2 copper layers, 104.0 x 39.5 mm, 13 parts (0 on the bottom side), 17 nets.

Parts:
ACELEROMETRO: GY-87; PinHeader_1x08_P2.54mm_Vertical
Arduino pro Mini: ARDUINO_PRO_MINI; MODULE_ARDUINO_PRO_MINI
BAT1: Pilas; PinHeader_1x02_P2.54mm_Vertical_SMD_Pin1Left
C1: 47uF; CP_Radial_D8.0mm_P3.50mm
Carg1: Cargador; SolderWire-0.25sqmm_1x03_P4.2mm_D0.65mm_OD1.7mm_Relief
D1: LED Blanco brillante; LED_D5.0mm
GPS: GPS_NEO_6; PinHeader_1x04_P2.54mm_Vertical
J2: LORA 868Mhz; PinHeader_1x07_P2.54mm_Vertical
J4: AEREO; PinHeader_1x02_P2.54mm_Vertical
JP1: JUMPER_CIRCUITO; PinHeader_1x02_P2.54mm_Vertical
R1: 220 Ohm; R_Axial_DIN0414_L11.9mm_D4.5mm_P7.62mm_Vertical
SW1: Interruptor general; R_Axial_Power_L20.0mm_W6.4mm_P5.08mm_Vertical
U2: ESP32-CAM

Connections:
3.3V: ACELEROMETRO.2 (3.3V), Arduino pro Mini.JP6_4 (VCC_1), GPS.4 (VCC), J2.7, JP1.2 (B)
3.7V: BAT1.1 (+), SW1.2 (B)
5V: Carg1.2, U2.P$1 (5V)
/CAMARA: Arduino pro Mini.JP7_4 (D6), U2.P$11 (IO3/U0R)
/GPS_RX: Arduino pro Mini.JP7_7 (D3), GPS.3 (RX)
/GPS_TX: Arduino pro Mini.JP7_6 (D4), GPS.2 (TX)
/LED: Arduino pro Mini.JP7_5 (D5), D1.2 (A)
/MISO: Arduino pro Mini.JP6_10 (MISO), J2.3
/MOSI: Arduino pro Mini.JP6_11 (MOSI), J2.2
/SCK: Arduino pro Mini.JP6_9 (SCK), J2.4
/SCL_ACE: ACELEROMETRO.4 (SCL), J4.2
/SDA_ACE: ACELEROMETRO.5 (SDA), J4.1
DIO0: Arduino pro Mini.JP7_8 (D2), J2.6
GND: ACELEROMETRO.3 (GND), Arduino pro Mini.JP1_5 (GND), Arduino pro Mini.JP1_6 (GND), Arduino pro Mini.JP6_2 (GND_1), Arduino pro Mini.JP7_9 (GND_2), BAT1.2 (-), C1.2, Carg1.1, GPS.1 (GND), J2.1, R1.2, U2.P$2 (GND)
NSS: Arduino pro Mini.JP6_12 (D10), J2.5
unnamed: C1.1, Carg1.3, JP1.1 (A), SW1.1 (A)
unnamed: D1.1 (K), R1.1

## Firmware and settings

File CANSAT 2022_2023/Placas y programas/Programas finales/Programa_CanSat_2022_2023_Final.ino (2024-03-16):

/*** - Programa CanSat 2022/2023 - ***/

/* Programa unificado para el proyecto CanSat 22/23
 * Dispositivo: ESP32 v4
 * Fecha creación: 23/10/22
 * Por Alejandro Chacón Pérez.
  */

/*        -=- Por hacer -=-
 * - Nada :D
 */

/*      -=- Changelog -=-
 * - 23/10/22 - Creación del proyecto
 * - 27/10/22 - Cambios en el programa: He quitado por ahora la librería del  LoRa y el GPS para no liarme y probar bien el GY-87.
 *              Añadida la funcionalidad del GY-87.
 * - 14/11/22 - Cambios para que funcione con la ESP32.
 * - 15/11/22 - Comienzo a añadir las funciones del LoRa 
 * - 17/11/22 - Añadida la función de concatenar los valores en una sola cadena. Queda probar el módulo LoRa
 *              con la ESP32 y la base estaría, aparte del buzzer opcional y el stepper de las semillas.
 * - 05/12/22 - Después del incidente del sensor, comienzo las pruebas del LoRa.
 * - 15/12/22 - Añadida la función del servo y limitados los delays en el loop principal. Ahora los mensajes del Serial van acompañados con un indicador visual.
 *              Ahora se envía el número de cadena para mantener mayor control.
 * - 19/12/22 - Prueba del módulo LoRa. En prinicipio no da error, aunque el servo ha parado de funcionar.
 * - 22/12/22 - EL problema del servo se ha arreglado poniendole la fuente de alimentación externa, con el adaptador para corriente. Añadidas las primeras funcionalidades de comunicación serial
 *              (Help y PinTest).
 * - 13/01/23 - Tras varios días con fallos con el módulo LoRa definitivo, ya funciona correctamente. La clave estaba en unos cortos en la antena y en inicializar tanto la placa y el sensor a la vez.
 *              Se debe usar la misma fuente para alimentar a ambos.
 * - 14/01/23 - Ajuste de comentarios y borrado código innecesario. Ahora la aceleración la saca haciendo el vector resultante de las 3 componentes, y no está limitado a una sola dirección.
 * - 16/03/23 - Versión 1.1: Añadida la función de mostrar la versión del programa. 
 * - 03/05/23 - Versión 2.0: Rematado todo. Añadida la comprobación de altura antes de abrir el servo. Limpiado de código. 
 * - 04/05/23 - Versión 2.1: Últimos ajustes de tiempos. Proyecto listo. 
 */ 

/*      -=- PinOut -=-
 * Servo →  4
 * MISO →   19  (Naranja))
 * MOSI →   23	(Amarillo)
 * SCK →    18  (Gris)
 * NSS →    5   (Morrarro)
 * RST →    26  (Azul)
 * DIO0 →   25  (Blanco)
 * SDA →    32  
 * SCL →    33  
*/

#include "Adafruit_BMP085.h"
#include "MPU6050.h"
#include "Wire.h"
#include "I2Cdev.h"
#include "LoRa.h"
#include "SPI.h"
#include "ESP32Servo.h"

#define LOOPTIME 2000
#define SERVOTIME 5000
#define SERVOTIME2 6000
#define ALTURADESCENSO 2
#define version "2.1"                                                                                       //Usamos #define para ahorrar variables innecesarias pero seguir podiendo cambiar los valores facilmente a la hora de editar.


Adafruit_BMP085 bmp;
MPU6050 sensor;
Servo servo1;                                                                                               //Objetos de los dos sensores y el servo.

long frecuency = 915E6;                                                                                     //Frecuencia del LoRa.
float temperatura = 99.99;
unsigned int presion = 999999;
float p0;                                                                                                   //Presión inicial.
float altura = 0;
float alturaPrev = 0;                                                                                       //Altura previa, para calcular cuándo mover el servo.
int cayendo;
float ace[3] = {+39.2, -39.2, +39.2};
float aceTotal;
float ang[3] = {-90, +90, -45.5};                                                                           //Variables para almacenar los valores de la aceleración y los ángulos.
short int ax, ay, az;
short int gx, gy, gz;                                                                                       // Valores sin procesar del acelarómetro y giroscopio.                                                                                                  // Valor de la presión inicial. Se toma al encender el CANSAT.
long tiempo_prev;
float dt;                                                                                                   // Variables que calculan el tiempo (Cálculos aceleromtro/giroscopio)
float ang_x, ang_y, ang_z;
float ang_x_prev, ang_y_prev, ang_z_prev;                                                                   //Variables para los cálculos del girsocopio.

long tiempo = 0;                                                                                            //Variable que controla los milisegundos pasados desde el encendido (Bucles).
long tiempoPrevServo;
bool extendido = false;                                                                                     //Variables de control del servo.
long tiempoPrevBucle;                                                                                       //Variable para el timer del bucle.

long ncadena = 0;                                                                                           //Variable del nº de cadena.

int leerSerial;                                                                                             //Variable para la lectura del puerto Serial.

//-----------------------------------------------------------------------------------------------------------------------------------------------------------------------------------------------------------------------------

void setup() {
  Serial.begin(9600);
  delay(4000);
  Serial.print(R"(  
                  - Programa CanSat 2022-2023 -

 |-| Software para el satelite del equipo Hexact para la edicion 2022-2023.
 |-| Vamos Luisma vamos!
 |-| Por Alejandro Chacon Perez :D
 |-| Version: )");
  Serial.println(version);
  Serial.println(" |-------------------------------------------------------------------------|");
  LoRa.setPins(5, 26, 25);                                                                                  //Pines para ss, reset y dio0 (ESP32 V1).
  //LoRa.setPins(18, 23, 26);                                                                               //Pines para ss, reset y dio0 (LILIGO T-Beam).
  if (LoRa.begin(frecuency)) {
    Serial.println(" |o| Modulo LoRa inciado correctamente.");
  }
  else{
    Serial.println(" |x| Error al iniciar el modulo LoRa.");
  }
  Wire.begin(32,33);
  sensor.initialize();
  if(sensor.testConnection()){                                                                              //Iniciamos sensores + posibles mensajes de error.
    Serial.println(" |o| Sensor MPU6050 iniciado correctamente (giroscopio).");
  }
  else{
    Serial.println(" |x| Error al iniciar el sensor MPU6050 (giroscopio).");
  }
  if(bmp.begin()){
    Serial.println(" |o| Sensor BMP180 iniciado correctamente (Temperatura + presion).");
  }
  else{
    Serial.println(" |x| Error al iniciar el sensor BMP180 (Temperatura + presion).");
  }
  servo1.attach(4);                                                                                         //Pin servo.
  servo1.write(150);
  p0 = bmp.readPressure();                                                                                  //Lectura de la presión inicial para calcular la altura relativa.
  Serial.print(" |i| Presioncilla inicial = ");
  Serial.println(p0);
  Serial.println(R"( |-------------------------------------------------------------------------|
 |H| Envia una 'h' o 'H' para recibir ayuda y una lista de comandos.
 |-------------------------------------------------------------------------|)");
  delay(500);
}

void leerGY87(){
  sensor.getAcceleration(&ax, &ay, &az);
  sensor.getRotation(&gx, &gy, &gz);                                                                        //Leemos los valores RAW de aceleración y angulos.
  dt = (millis()-tiempo_prev)/1000.0;
  tiempo_prev = millis();                                                                                   //Calculamos el tiempo pasado entre cada medición. 
  float ang_x_accel = atan(ax/sqrt(pow(ay,2) + pow(az,2)))*(180.0/3.14);
  float ang_y_accel = atan(ay/sqrt(pow(az,2) + pow(ax,2)))*(180.0/3.14);
  float ang_z_accel = atan(az/sqrt(pow(ax,2) + pow(ay,2)))*(180.0/3.14);
  ang_x = 0.98*(ang_x_prev+(gx/131)*dt) + 0.02*ang_x_accel;
  ang_y = 0.98*(ang_y_prev+(gy/131)*dt) + 0.02*ang_y_accel;
  ang_z = 0.98*(ang_z_prev+(gy/131)*dt) + 0.02*ang_z_accel;                                                 //Calculamos la rotación usando tanto el girsocopio como el acelerómetro para eliminar errores.
  ang_x_prev = ang_x;
  ang_y_prev = ang_y;
  ang_z_prev = ang_z;
  ace[2] = az * (9.81/16384.0);
  ace[1] = ay * (9.81/16384.0);
  ace[0] = ax * (9.81/16384.0);                                                                             //Calculamos la aceleración en m/s2 en los tres ejes 
  ang[0] = ang_x_accel;  
  ang[1] = ang_y_accel;
  ang[2] = ang_z_accel;
  alturaPrev = altura;
  altura = bmp.readAltitude(p0);
  Serial.println(altura);
  Serial.println(alturaPrev);
  presion = bmp.readPressure();
  temperatura = bmp.readTemperature();                                                                      //Leemos el resto de datos necesarios.
  aceTotal = sqrt((pow(ace[0], 2)) + (pow(ace[1], 2)) + (pow(ace[2], 2)));                                  //Calculamos la aceleración total. 
}

void crearCadena(){
  char cadena [48] = "";
  snprintf(cadena, sizeof(cadena), "$%ld?%.2f?%.2f?%.2f?%.2f?%d?%.2f#", ncadena, ang[0], ang[1], aceTotal, temperatura, presion, altura); //Formateamos los valores a enviar en 1 sola cadena.
  //Cadena max = $9999?-99.99?-99.99?-99.99?-99.99?999999?-999.9#
  Serial.print(" |>| Cadena para enviar: ");  
  Serial.println(cadena);
  ncadena = ncadena + 1;                                                                                    //Actualizamos el contador de cadenas enviadas. 
  LoRa.beginPacket();
  LoRa.print(cadena);
  LoRa.endPacket();                                                                                         //Enviamos el paquete y cerramos transmisión.
}

void loop() {
  while(Serial.available() > 0){                                                                            //Escuchamos el Serial por si recibimos algún comando.
    leerSerial = Serial.read();
    if((leerSerial == 'p') || (leerSerial == 'P')){                                                         //Si es una P, ejecutamos un testeo de sensores.
      Serial.println(R"( |-----------------------------------------------------------------|
 |P| Prueba de conexion. )");
      if(sensor.testConnection()){
        Serial.println(" |o| Sensor MPU6050 conectado correctamente (giroscopio).");
      }
      else{
        Serial.println(" |x| Error al conectar el sensor MPU6050 (giroscopio).");
      }
      if(bmp.begin()){
        Serial.println(" |o| Sensor BMP180 conectado correctamente (Temperatura + presion).");
      }
      else{
        Serial.println(" |x| Error al conectar el sensor BMP180 (Temperatura + presion).");
      }
      Serial.println(" |-----------------------------------------------------------------|");
    }
    else if ((leerSerial == 'h') || (leerSerial == 'H')){                                                   //Si es una H, enviamos el pinout, la frecuencia, y otros comandos. 
      Serial.print(R"( |--------------------------------------------|
 |H| PinOut:
 |   Servo -> 4
 |   MISO --> 19
 |   MOSI --> 23	
 |   SCK ---> 18
 |   NSS ---> 5
 |   RST ---> 26
 |   DIO0 --> 25
 |   SDA ---> 21
 |   SCL ---> 22
 |--------------------------------------------|
 |i| Frecuencia actual = )");
      Serial.println(frecuency);
      Serial.println(" |--------------------------------------------|");
      Serial.println(R"( |H| Otros comandos:
 |   's' o 'S' -> Alterna el estado del servo.
 |   'p' o 'P' -> Prueba de sensores.
 |   'h' o 'H' -> Comando de ayuda (Este).
 |--------------------------------------------|)");
    }
    else if ((leerSerial == 's') ||  (leerSerial == 'S')){                                                  //Si es una s, alterna el estado del servo (Extendido <-> Retraido).
      switch (extendido){
        case true:
          servo1.write(170);
          Serial.println(" |!| Servo en retraccion.");
          break;
        case false:
          servo1.write(55);
          Serial.println(" |!| Servo en extension.");
          break;
      }
      extendido = !extendido;
    }
  }
  tiempo = millis();                                                                                        //Leemos los milisegundos pasados para controlar los bucles. 
  if((alturaPrev >= (altura + ALTURADESCENSO)) && (tiempo >= tiempoPrevBucle + LOOPTIME)){                               //Si la altura anterior es igual o mayor que la altura nueva mas 1m, quire decir que estamos cayendo, por lo que aumentamos 1 al contador
    cayendo = cayendo + 1;                                                                                  //(Contador para comprobar que estamos cayendo 2 veces mínimo, y evitar posibles errores.)
    Serial.println(cayendo);
  }                                    
  if((tiempo >= tiempoPrevServo+ SERVOTIME) && (extendido == false) && (cayendo >= 2)){                     //Extendemos el servo si ha pasado el tiempo establecido...
    Serial.println(" |!| Servo en extension.");
    servo1.write(55);
    extendido = true;
  }

  if((tiempo  >= tiempoPrevServo + SERVOTIME2) && (cayendo >= 2)){                                          //...y lo retraemos si ha pasado el 2º tiempo.
    Serial.println(" |!| Servo en retraccion.");
    servo1.write(150);
    tiempoPrevServo = tiempo;
    extendido = false;
  }

  if(tiempo >= tiempoPrevBucle + LOOPTIME){                                                                 //Función de bucle para evitar las interrupciones del delay.
    leerGY87();  
    crearCadena();
    tiempoPrevBucle = tiempo;
  }
}

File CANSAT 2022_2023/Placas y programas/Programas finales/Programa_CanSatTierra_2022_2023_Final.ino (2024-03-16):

/*** CanSat 2022-2023 Estación de tierra ***/

/* Programa unificado para el proyecto CanSat 22/23
 * Dispositivo: LilyGo T-Beam v1.1
 * Fecha creación: ??/10/22
 * Por Alejandro Chacón Pérez
*/

 /*       -=- PinOut -=-
 MISO --> 4
 MOSI --> 13	
 CLK ---> 14
 CS ----> 2
 SDA ---> 21
 SCL ---> 22
 */

/*      -=- Changelog -=-
 * - ??/10/22 - Creación del proyecto.
 * - 21/11/22 - Finalizada la función de desencriptación de valores de la cadena. Investigar si se puede hacer sin clase String (Spoiler: Si, pero es tarde).
 * - 28/11/22 - Finalizada (otra vez) la función de desencriptar los valores de la cadena. Añadidos detalles para la pantalla. Solo queda añadir la radio y la SD para la versión 1.0 :D
 * - 24/12/22 - Añadida la primera iteración de la señal de nueva cadena recibida. 
 * - 29/12/22 - Finiquitada la función demostrar potencia y cuando llega una cadena nueva.
 * - 13/01/23 - Corrección de algunos errores con los iconos de la potencia.
 * - 14/01/23 - Añadida funcionalidad GPS. Añadidas pantallas de latitud, longitud, nº de satélites y voltaje de la batería. Añadido reloj en la esquina inferior  derecha. V 1.0 lista. 
 * - 18/04/23 - Eliminada la función de borrar el documento, ahora sigue escribiendo encima para no perder data. Añadida la función de guardar la posición GPS en la SD. 
                Añadida la función de la versión en la pantalla de inicio. v 1.1 lista
 * - 19/04/23 - Versión 1.2. Ajustes a la UI.
 * - 23/04/23 - Versión 1.3. Añadida funcionalidad rudimentaria para obtener la disstancia según la RSSI. Añadidos valores para las 3 antenas, cambiable sólo a través de código. 
 * - 24/04/23 - Versión 1.4. Añadida la función de cambiar de antena desde la propia estación, con la pulsación corta-larga. 
 * - 26/04/23 - Versión 1.5. Añadida el almacenamiento y lectura del nº de antena en la EEPROM, para así no tener que volver a configurarlo cada vez que se resetea. Lo mismo con el InvertDisplay.
 * - 03/05/23 - Versiones 1.6 y 1.7: Cambiadas las fórmulas de distancias. 
 * - 04/05/23 - Versión 2.0: Todo finalizado. Aún hay cosass que no entiendo, pero así se quedan. Paso de todo :D.
 */ 


#include <SPI.h>
#include <Wire.h>
#include <Adafruit_GFX.h>
#include <Adafruit_SSD1306.h>
#include <LoRa.h>
#include <axp20x.h>
#include <TinyGPS++.h>
#include <SD.h>
#include <EEPROM.h>

#define SCREEN_WIDTH 128                                                                                    // Ancho del display.
#define SCREEN_HEIGHT 64                                                                                    // Alto del display.

#define logo_HEIGHT 30                                                                                      //Alto del logo.
#define logo_WIDTH 30                                                                                       //Ancho del logo

const unsigned char logo [] PROGMEM = {                                                                     //Array de bits para las distintas imagenes.
	0x00, 0x00, 0x00, 0x00, 0x00, 0x00, 0x00, 0x00, 0x00, 0x00, 0x00, 0x00, 0x00, 0x00, 0x00, 0x00, 
	0x00, 0x07, 0x80, 0x00, 0x00, 0x1c, 0xe0, 0x00, 0x00, 0x31, 0xf0, 0x00, 0x00, 0xc7, 0x1c, 0x00, 
	0x03, 0x9c, 0x07, 0x00, 0x07, 0x38, 0x11, 0x80, 0x07, 0x38, 0x1c, 0x80, 0x07, 0x38, 0x46, 0x80, 
	0x07, 0x38, 0x73, 0x80, 0x07, 0x38, 0x73, 0x80, 0x07, 0x3e, 0x73, 0x80, 0x07, 0x38, 0xf3, 0x80, 
	0x07, 0x38, 0x73, 0x80, 0x07, 0x38, 0x73, 0x80, 0x05, 0x18, 0x73, 0x80, 0x04, 0xc0, 0x73, 0x80, 
	0x04, 0x60, 0x73, 0x80, 0x03, 0x00, 0x63, 0x00, 0x01, 0xc1, 0xce, 0x00, 0x00, 0x67, 0x38, 0x00, 
	0x00, 0x1c, 0x60, 0x00, 0x00, 0x0f, 0xc0, 0x00, 0x00, 0x03, 0x00, 0x00, 0x00, 0x00, 0x00, 0x00, 
	0x00, 0x00, 0x00, 0x00, 0x00, 0x00, 0x00, 0x00
};

const unsigned char signal0 [] PROGMEM = {
	0x00, 0x00, 0x3c, 0x00, 0x00, 0x24, 0x00, 0x00, 0x24, 0x00, 0x0f, 0x24, 0x00, 0x09, 0x24, 0x00, 
	0x09, 0x24, 0x03, 0xc9, 0x24, 0x02, 0x49, 0x24, 0x02, 0x49, 0x24, 0xf2, 0x49, 0x24, 0x92, 0x49, 
	0x24, 0x92, 0x49, 0x24, 0x92, 0x49, 0x24, 0x92, 0x49, 0x24, 0x92, 0x49, 0x24, 0xf3, 0xcf, 0x3c
};

const unsigned char signal1 [] PROGMEM = {
	0x00, 0x00, 0x3c, 0x00, 0x00, 0x24, 0x00, 0x00, 0x24, 0x00, 0x0f, 0x24, 0x00, 0x09, 0x24, 0x00, 
	0x09, 0x24, 0x03, 0xc9, 0x24, 0x02, 0x49, 0x24, 0x02, 0x49, 0x24, 0xf2, 0x49, 0x24, 0xf2, 0x49, 
	0x24, 0xf2, 0x49, 0x24, 0xf2, 0x49, 0x24, 0xf2, 0x49, 0x24, 0xf2, 0x49, 0x24, 0xf3, 0xcf, 0x3c
};

const unsigned char signal2 [] PROGMEM = {
	0x00, 0x00, 0x3c, 0x00, 0x00, 0x24, 0x00, 0x00, 0x24, 0x00, 0x0f, 0x24, 0x00, 0x09, 0x24, 0x00, 
	0x09, 0x24, 0x03, 0xc9, 0x24, 0x03, 0xc9, 0x24, 0x03, 0xc9, 0x24, 0xf3, 0xc9, 0x24, 0xf3, 0xc9, 
	0x24, 0xf3, 0xc9, 0x24, 0xf3, 0xc9, 0x24, 0xf3, 0xc9, 0x24, 0xf3, 0xc9, 0x24, 0xf3, 0xcf, 0x3c
};

const unsigned char signal3 [] PROGMEM = {
	0x00, 0x00, 0x3c, 0x00, 0x00, 0x24, 0x00, 0x00, 0x24, 0x00, 0x0f, 0x24, 0x00, 0x0f, 0x24, 0x00, 
	0x0f, 0x24, 0x03, 0xcf, 0x24, 0x03, 0xcf, 0x24, 0x03, 0xcf, 0x24, 0xf3, 0xcf, 0x24, 0xf3, 0xcf, 
	0x24, 0xf3, 0xcf, 0x24, 0xf3, 0xcf, 0x24, 0xf3, 0xcf, 0x24, 0xf3, 0xcf, 0x24, 0xf3, 0xcf, 0x3c
};

const unsigned char signal4 [] PROGMEM = {
	0x00, 0x00, 0x3c, 0x00, 0x00, 0x3c, 0x00, 0x00, 0x3c, 0x00, 0x0f, 0x3c, 0x00, 0x0f, 0x3c, 0x00, 
	0x0f, 0x3c, 0x03, 0xcf, 0x3c, 0x03, 0xcf, 0x3c, 0x03, 0xcf, 0x3c, 0xf3, 0xcf, 0x3c, 0xf3, 0xcf, 
	0x3c, 0xf3, 0xcf, 0x3c, 0xf3, 0xcf, 0x3c, 0xf3, 0xcf, 0x3c, 0xf3, 0xcf, 0x3c, 0xf3, 0xcf, 0x3c
};

const unsigned char signal5 [] PROGMEM = {
	0x00, 0x00, 0x00, 0x07, 0x03, 0x80, 0x18, 0x00, 0x60, 0x00, 0x00, 0x00, 0x1f, 0x03, 0xe0, 0x11, 
	0x02, 0x20, 0x11, 0x22, 0x20, 0x11, 0x22, 0x20, 0x1f, 0x13, 0xe0, 0x00, 0x20, 0x00, 0x00, 0x00, 
	0x40, 0x00, 0x00, 0x20, 0x01, 0xfe, 0x20, 0x03, 0x03, 0x00, 0x02, 0x01, 0x00, 0x00, 0x00, 0x00
};

const unsigned char sd1 [] PROGMEM = {
	0x00, 0x00, 0x0f, 0xf0, 0x1d, 0x50, 0x35, 0x50, 0x75, 0x50, 0x77, 0xf0, 0x3f, 0xf0, 0x3f, 0xf0, 
	0x3f, 0xf0, 0x77, 0x70, 0x7a, 0xf0, 0x7d, 0xf0, 0x7a, 0xf0, 0x77, 0x70, 0x7f, 0xf0, 0x7f, 0xf0, 
	0x7f, 0xf0, 0x00, 0x00
};

const unsigned char sd2 [] PROGMEM = {
	0x00, 0x00, 0x0f, 0xf0, 0x1d, 0x50, 0x35, 0x50, 0x75, 0x50, 0x77, 0xf0, 0x3f, 0xf0, 0x3f, 0xf0, 
	0x3f, 0xf0, 0x7f, 0xb0, 0x7f, 0x30, 0x6e, 0x70, 0x64, 0xf0, 0x71, 0xf0, 0x7b, 0xf0, 0x7f, 0xf0, 
	0x7f, 0xf0, 0x00, 0x00
};




const int boton = 38;                                                                                       //Pin boton.

int leerSerial;                                                                                             //Variable para la lectura del Serial.

bool invertDisplay = false;                                                                                 //Variable para invertir la pantalla.

int screen = 0;                                                                                             //Control de pantallas (Qué pantalla se está mostrando en cada momento.)
int antenna = 3;
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

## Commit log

2024-03-16 CANSAT 2022_2023
    Proyecto CANSAT del año 2022_2023
    [ANTENAS.stl, Archivo CSV.csv, Archivo CSV_Visor de GNSS.xlsx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]
2024-03-16 CANSAT 2021_2022
    Informe crítico de diseño y material del lanzamiento en 2022. Puebla del Río.
    [Base_Antena_mejorada.stl, Base_antena.3mf, Base_antena.FCStd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]
